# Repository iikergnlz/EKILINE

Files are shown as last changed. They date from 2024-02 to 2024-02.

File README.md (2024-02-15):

# EKILINE

Proiektu honek bi gurpileko robot orekatzaile bat da (balancing), zutik mantendu behar da modulu giroskopiko bati esker, aldi berean, lerro bat jarrai baitezake sentsore batzuei esker.
Horretarako hainbat pauso jarraitu ditugu.

# JARRAITU BEHAR DIREN URRATSAK:

  1.- Gure proiektuarekin hasteko, solairu bakoitza inprimatu izan behar genuen 3D inprimagailu bat erabiliz, ultimaker cura aplikazioaren bidez, 3 pieza inprimatu genuen:

Captura de pantalla (5)29
    ** Plaken artxiboa goian dago

  1.1.- Bestalde, 3D inprimagailuan ere gurpilak inprimatuko ditugu:

  Captura de pantalla (7)
  ** Gurpilen artxiboa goian dago

  2.- Egitura muntatu: 
      Orain, egitura osoa muntatuko dugu; lehenik, gomak gurpiletan jarriko ditugu (horietan hobeto heltzeko); orain, 3 solairuko egitura muntatuko dugu, aurrez inprimatutako plakekin;         M3ko barrak, 24 azkoinak eta azkoinaren azken 8ak erabiliko ditugu.

  3.- Plakak diseinatu eta fresatu (Konexioak, Sentsoreak eta Potentzia etapa):

  3.1.- Konexioak: Plaka honetan hainbat konponente erabili ditugu, hala nola, Teensy 4.0, DRV8834, MPU6050, Bluetooth HC-05, Kondentsadoreak, Bornak eta Zokaloak.             Honen neurriak hauek dira, 6.5 cm-ko zabalera eta 13 cm-ko luzera du. Honekin batera, eskema elektrikoko eta pcb-ko argazkiak doaz, bai eta artxiboko argazkiak         ere, deskargatu ahal izateko.
 
Captura de pantalla (8)

Captura de pantalla (9)

  3.2.- Sentsoreak: Plaka honetan multiplexore bat erabili dugu, zehazki, 74HC4067-a. Gainera, marra jarraitu ahal izateko 16 sentsore erabili ditugu, qre1113gr-ak eta
        guzti hau Teensy-ra konektatu ditugu konektore batzuen bidez.
        
Captura de pantalla (10)

        Hemen dago Plakaren PCB-a:
        
Captura de pantalla (11)

    3.2.- Potentzia etapa: Era berean, gure plakari potentzia-kontrol bat gehitu diogu teensya elikatu ahal izateko, 12V - 5V bihurtuz.

Captura de pantalla (40)

          Hemen dakagu PCB-a:
          
Captura de pantalla (39)

    4.-Eta orain dena kableen bidez konektatzea besterik ez da geratzen, eta azken emaitzak honen antzeko zerbait izan         beharko luke, 3 bistetan ikusita:
IMG-20240215-WA0001
IMG-20240215-WA0000
IMG-20240215-WA0002

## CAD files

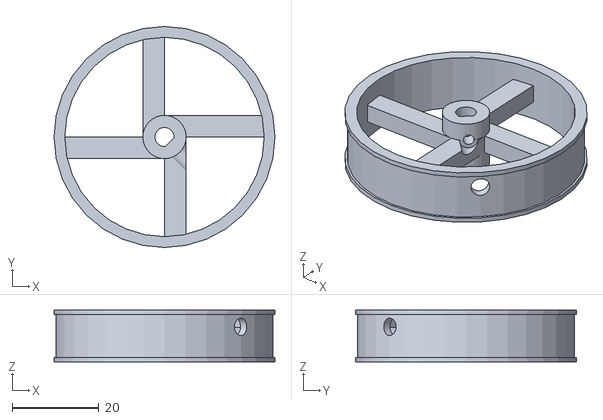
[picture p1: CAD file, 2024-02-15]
Wheel.stl
51.0 x 51.0 x 12.0

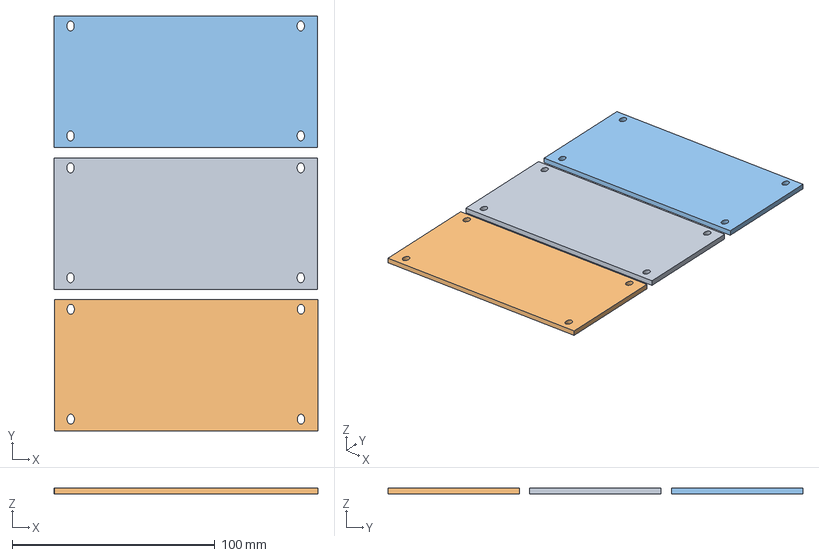
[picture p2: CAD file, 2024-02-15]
placa defi.3mf
130.1 x 204.8 x 2.93 mm
Top_plate.stl
Top_plate.stl(1)
Top_plate.stl(2)

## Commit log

2024-02-14 Beharrezko materialak
2024-02-15 Update Beharrezko materialak
